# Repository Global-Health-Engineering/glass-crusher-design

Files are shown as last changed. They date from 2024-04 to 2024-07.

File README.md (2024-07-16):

<!-- badges: start -->


<!-- badges: end -->

<h1> Low-Cost Glass Crusher for Cape Maclear, Malawi: Design, Maintenance, Operation, and Results </h1>

<b>Contributors</b>  
- Philippe Colbach <a href="https://orcid.org/0009-0004-5631-8744">
ORCID logo 0009-0004-5631-8744
</a> *author, maintainer*  
- Jakub Tkaczuk <a href="https://orcid.org/0000-0001-7997-9423">
ORCID logo 0000-0001-7997-9423
</a> *supervisor, developer*  
- Elizabeth Tilley <a href="https://orcid.org/0000-0002-2095-9724">
ORCID logo 0000-0002-2095-9724
</a> *supervisor*  

<br>
<p align="middle"> 

<br><br>
This work is certified by the Open Source Hardware Association.<br \>

<br>
<b>Complete description of system design, functionalities, operation, and maintenance is available on:<br \>
<a href="https://global-health-engineering.github.io/glass-crusher-design/">Github pages</a>.
</b>
<br><br>
It compliments the openly-accessible master’s thesis, available on the<br \>  
<a href="http://hdl.handle.net/20.500.11850/670971">ETH Research Collection</a>.
</p>

# Background

This repository details the construction, operation, and maintenance of the glass crusher built as part of a collaboration between the Malawian nonprofit organization, Sustainable Cape Maclear, and the Global Health Engineering Group at ETH Zürich.

Sustainable Cape Maclear has been working on the development and implementation of a solid waste management strategy to address the village’s struggle with waste build-up at informal dumpsites. The desired outcome is an improved quality of life for the community and the preservation of the village’s status quo as one of the country’s major tourist destinations. To support the effort, the glass crusher, described in this repository, was designed, constructed and tested as a part of the Master's thesis.

After evaluating already established glass crusher variants, the design of choice became a manually driven roller mill. During testing, the drivetrain proved to be a major weak point. Due to its insufficient structural strength, the crusher was unable to crush intact glass bottles. However, breaking the bottles first and inserting their shards into the crusher worked well, producing particles of various sizes ranging from powder to several centimeters. Therefore, a second and more basic crusher, not described in this repository but detailed in the thesis, was built to take over the initial bottle-breaking task. The latter can serve as a standalone crusher, if large shard sizes are sufficient, or it can be combined with the original crusher, if smaller sizes are desired. In hindsight, it would have been better to build a more basic and robust crusher right from the start to circumvent many of the issues that arose. Overall, the current system is nonetheless capable of processing the village’s daily amount of waste glass within an acceptable time frame.

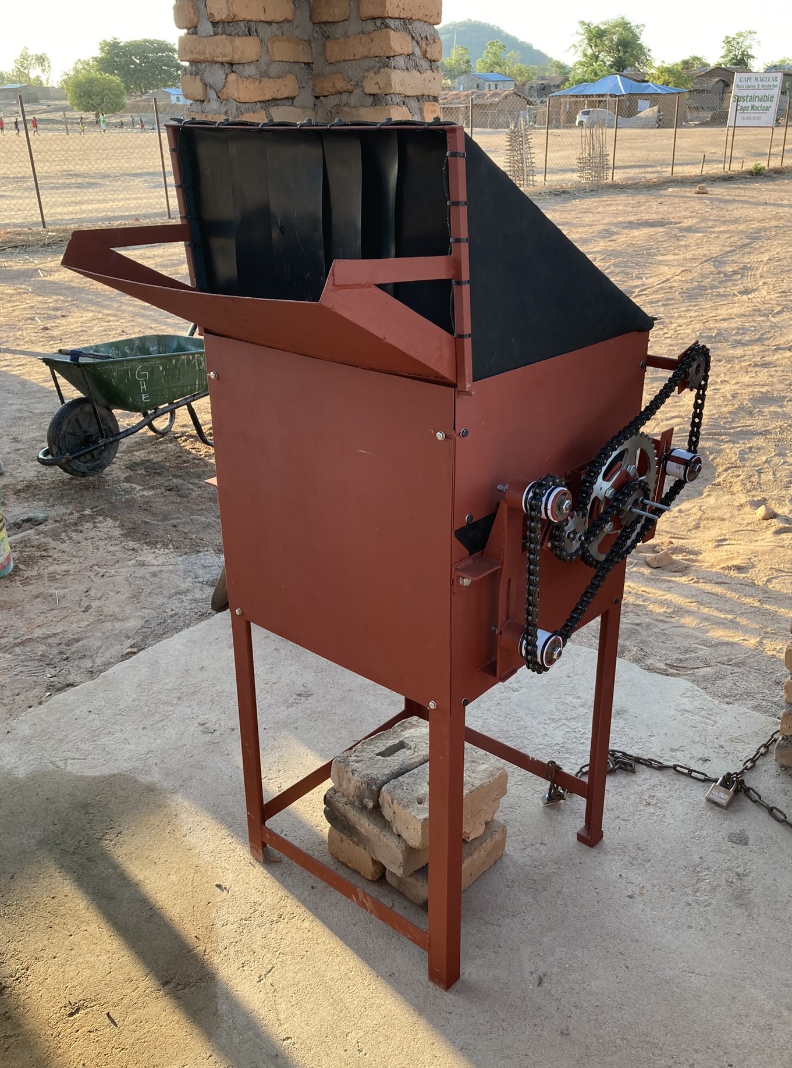
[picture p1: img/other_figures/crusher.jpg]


# pdf Documentation

All drawings necessary for the glass crusher construction are available in a pdf form in `pdf_doc/Glass_Crusher_Complete_Collection_of_Technical_Drawings.pdf`.

# License

The complete design and user manual are licensed under [Creative Commons Attribution 4.0 International](https://github.com/Global-Health-Engineering/glass-crusher-design/blob/main/LICENSE.md).

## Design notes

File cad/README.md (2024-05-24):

# cad

Directory containing CAD drawings in `.stp`, `.prt`, and `.pdf` formats.

| `dir` name | Description |
| --- | --- |
| `A_Glass_Crusher_Full_Assembly.*` | Final assembly of the glass crusher in three formats |
| `standard_parts` | Drawings of standard parts, e.g., screws, nuts, washers |
| `sub-assemblies` | All subassemblies used in `A_Glass_Crusher_Full_Assembly.stp` |
| `sub-assemblies/cover` | Drawings of the crusher's cover |
| `sub-assemblies/extended_frame` | Drawings of the assembled, extended frame |
| `sub-assemblies/motorcycle_chains` | Drawings of the motorcycle chain |
| `sub-assemblies/roller_mounting_platform` | Drawings of the roller mounting platform |
| `sub-assemblies/rollers` | Drawings of the rollers |
| `sub-assemblies/sprocket_module_large` | Drawings of the large sprocket module |
| `sub-assemblies/sprocket_module_small` | Drawings of the small sprocket module |
| `sub-assemblies/upper_side_panels` | Drawings of the upper side panels |

Each directory with an assembly contains the `parts` directory with the simplest part drawings.

# tree

    .
    ├── A_Glass_Crusher_Full_Assembly.prt
    ├── A_Glass_Crusher_Full_Assembly.stp
    ├── A_Glass_Crusher_Full_Assembly_dwg.pdf
    ├── standard_parts
    └── sub-assemblies
        ├── cover
        │   └── parts
        ├── extended_frame
        │   ├── parts
        │   └── subassemblies
        │       ├── crank
        │       │   └── parts
        │       ├── crank_side_panel
        │       │   └── parts
        │       ├── drivetrain_panel
        │       │   ├── parts
        │       │   └── subassemblies
        │       │       └── chain_guides
        │       │           └── parts
        │       └── frame
        │           └── parts
        ├── motorcycle_chains
        │   └── subassemblies
        │       └── chain_subunits
        │           └── parts
        ├── roller_mounting_platform
        │   └── parts
        ├── rollers
        │   ├── parts
        │   └── subassemblies
        │       └── roller_bearing_brackets
        │           └── parts
        ├── sprocket_module_large
        │   └── parts
        ├── sprocket_module_small
        │   └── parts
        └── upper_side_panels
            └── parts

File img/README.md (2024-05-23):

# img

This directory contains images grouped into following sub-directories:

| `dir` name | Description |
| --- | --- |
| `drawings` | Engineering drawings of parts and assemblies |
| `other_figures` | Figures and photographs for technical documentation |

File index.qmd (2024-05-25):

---
title: "Low-Cost Glass Crusher for Cape Maclear, Malawi"
subtitle: "Design, Maintenance, Operation, and Results"
number-sections: true
format: html
---

<!-- badges: start -->


<!-- badges: end -->

<b>Contributors:</b>  
- Philippe Colbach <a href="https://orcid.org/0009-0004-5631-8744">
ORCID logo 0009-0004-5631-8744
</a> *author, maintainer*  
- Jakub Tkaczuk <a href="https://orcid.org/0000-0001-7997-9423">
ORCID logo 0000-0001-7997-9423
</a> *supervisor, developer*  
- Elizabeth Tilley <a href="https://orcid.org/0000-0002-2095-9724">
ORCID logo 0000-0002-2095-9724
</a> *supervisor*  

<br>
<p align="middle">

<br><br> This work is certified by the Open Source Hardware
Association.\
(https://certification.oshwa.org/ch000022.html)
<br>
Github repository for this page sits [here](https://github.com/Global-Health-Engineering/glass-crusher-design).
</p>

# Introduction {#sec-intro}

This documentation details the construction, operation, and maintenance of the glass crusher that was built as part of a collaboration between the Malawian nonprofit organization Sustainable Cape Maclear and the Global Health Engineering Group at ETH Zürich.

# Prototype Overview {#sec-overview}

The glass crusher uses two roller mills to crush the glass. The rollers are rotated using a crank and a drivetrain made mostly from motorcycle parts. It is a mostly closed construction to shield the operator(s) from glass dust and shards.

Figure 1: Complete assembly of the glass crusher.

During testing, it became clear that the crusher was not strong enough to break intact glass bottles. Therefore, an additional pre-crusher was built to break the bottles first before inserting their shards into the main crusher for further refinement.

Unless explicitly stated otherwise, all information in this documentation relates to the main glass crusher, not the pre-crusher.

# Part List {#sec-list}

| Material | Units | Unit Cost (MWK) | Total Cost (MWK) | Total Cost (USD) | Notes |
| :--- | ---: | ---: | ---: | ---: | --- |
| Anti-Rust Coating <br> 1 L | 1 | 26'000 | 26'000 | 14.77 | |
| Bearing 6206 RS <br> Ø<sub>i</sub> 30 mm | 2 | 9'000 | 18'000 | 10.23 | |
| Bearing 6304 2RS <br> Ø<sub>i</sub> 20 mm | 2 | 8'000 | 16'000 | 9.09 | |
| Damp-proof course <br> 0.25 mm x 100 mm x 40'000 mm | 1 | 4'950 | 4'950 | 2.81 | |
| Durable rubber sheet <br> 2 mm x 1'500 mm x 2'600 mm | 1 | 70'000 | 70'000 | 39.77 | |
| Galvanized steel elbow connector <br> Ø<sub>i</sub> 15 mm | 2 | 1'024 | 2'048 | 1.16 | |
| Galvanized steel pipe <br> Ø<sub>i</sub> 15 mm x Ø<sub>o</sub> 20 mm x 1'000 mm | 1 | 16'174 | 16'174 | 9.19 | |
| Galvanized steel pipe <br> Ø<sub>i</sub> 15 mm x Ø<sub>o</sub> 20 mm x 300 mm | 2 | 5'044 | 10'088 | 5.73 | |
| Galvanized steel round cap <br> Ø<sub>i</sub> 15 mm | 1 | 734 | 734 | 0.42 | |
| L-profile <br> 5 mm x 40 mm x 40 mm x 5'800 mm | 1 | 39'500 | 39'500 | 22.44 | |
| Motorcycle Chain <br> Size 520 x 66 links (minimum) | 2 | 70'000 | 140'000 | 79.55 | |
| Motorcycle Sprocket <br> Size 520 x 13T | 3 | 28'000 | 84'000 | 47.73 | |
| Motorcycle Sprocket <br> Size 520 x 42T | 1 | 65'000 | 65'000 | 36.93 | |
| PVC pipe <br> Ø<sub>i</sub> 22 mm x Ø<sub>o</sub> 25 mm x 3'000 mm | 1 | 3'300 | 3'300 | 1.88 | |
| PVC straight pipe connector <br> Øi 50 mm x 50 mm | 3 | 1'200 | 3'600 | 2.05 | |
| Screws, nuts, and washers[^1] | 1 | 49'600 | 49'600 | 28.18 | |
| Steel bar flat <br> 2.75 mm x 20 mm x 5'800 mm | 1 | 6'000 | 6'000 | 3.41 | |
| Steel corner bracket <br> 2.5 mm x 50 mm x 50 mm x 20 mm | 1 | 604 | 604 | 0.34 | |
| Steel flat bar <br> 5 mm x 40 mm x 5'800 mm | 1 | 45'000 | 45'000 | 25.57 | |
| Steel pipe <br> Ø<sub>o</sub> 43 mm x 1'000 mm | 1 | 0 | 0 | 0.00 | scrap part |
| Steel roller <br> Ø<sub>o</sub> 150 mm x 500 mm | 2 | 209'700 | 419'400 | 238.30 | |
| Steel sheet <br> 2 mm x 1'300 mm x 3'350 mm | 1 | 250'000 | 250'000 | 142.05 | |
| Steel sheet <br> 3 mm x  350 mm x 400 mm | 1 | 0 | 0 | 0.00 | scrap part |
| Steel square tubing <br> 1.15 mm x 15 mm x 15 mm x 5'800 mm | 2 | 4'950 | 9'900 | 5.63 | |
| Zip ties | 33 | 0 | 0 | 0.00 | scrap part |
|  |  | **TOTAL COST** | **1'279'898** | **727.21** | |

[^1]: 24 x screw M6 x 16, 1 x screw M6 x 20, 2 x screw M6 x 25, 12 x screw M6 x 30, 4 x screw M6 x 45, 2 x stud M6 x 20, 53 x nut M6, 67 x washer M6, 5 x screw M10 x 20 <br> 12 x screw M10 x 30, 1 x stud M10 x 90, 2 x stud M10 x 120, 23 x nut M10, 19 x washer M10

# Safety Precautions {#sec-safety}

Always wear protective equipment when working with glass. A mask, goggles, gloves and closed footwear are essential for protecting the operator’s health.

# License {#sec-license}

The complete design and user manual are licensed under [Creative Commons Attribution 4.0 International](https://github.com/Global-Health-Engineering/glass-crusher-design/blob/main/LICENSE.md).

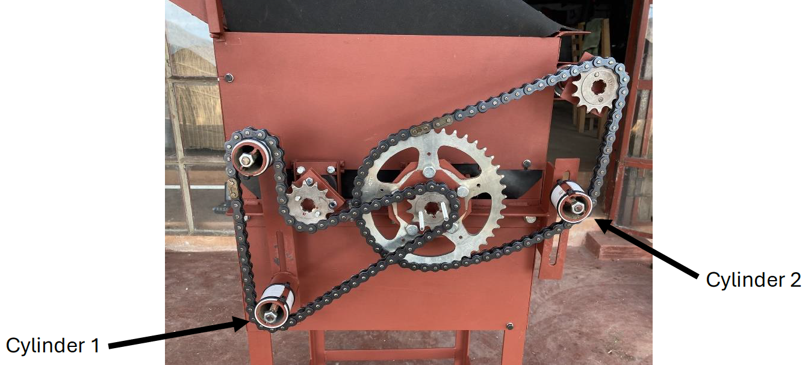
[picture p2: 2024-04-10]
docs/img/schematics/chain-replacement-cylinders.png

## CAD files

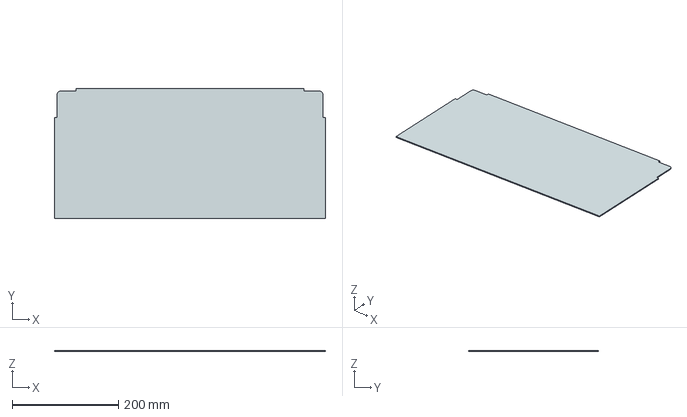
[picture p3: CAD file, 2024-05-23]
cad/sub-assemblies/extended_frame/subassemblies/frame/parts/M_Bot_Funnel_Panel_Main.stp
510.0 x 245.0 x 2.00 mm

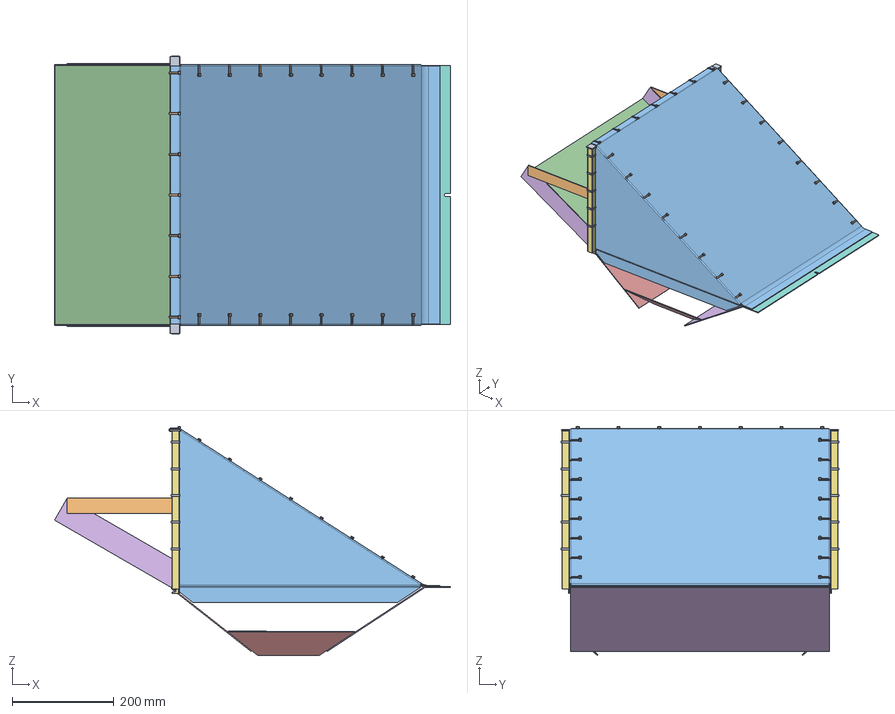
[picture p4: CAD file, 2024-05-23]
cad/sub-assemblies/cover/A_Cover.stp
779.5 x 547.0 x 450.8 mm
M_Zip_Tie_Symbolic_Square x 10
M_Zip_Tie_Symbolic_Flat x 23
FlatPattern_Geometry x 7
M_Top_Funnel_Side x 2
M_Chute_Side x 2
M_Cover_Support_Mirror
M_Top_Funnel_Support
M_Cover_Crossbar
M_Chute_Support x 2
M_Cover_Strut x 2
M_Chute_Plate
M_Cover_Support
M_Top_Funnel_Plate_S
M_Top_Funnel_Plate_L

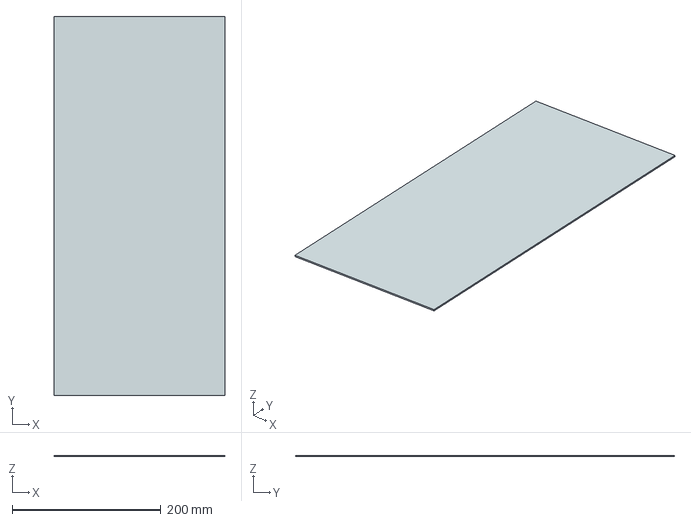
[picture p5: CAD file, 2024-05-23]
cad/sub-assemblies/cover/parts/M_Top_Funnel_Plate_L.stp
230.0 x 510.0 x 2.00 mm

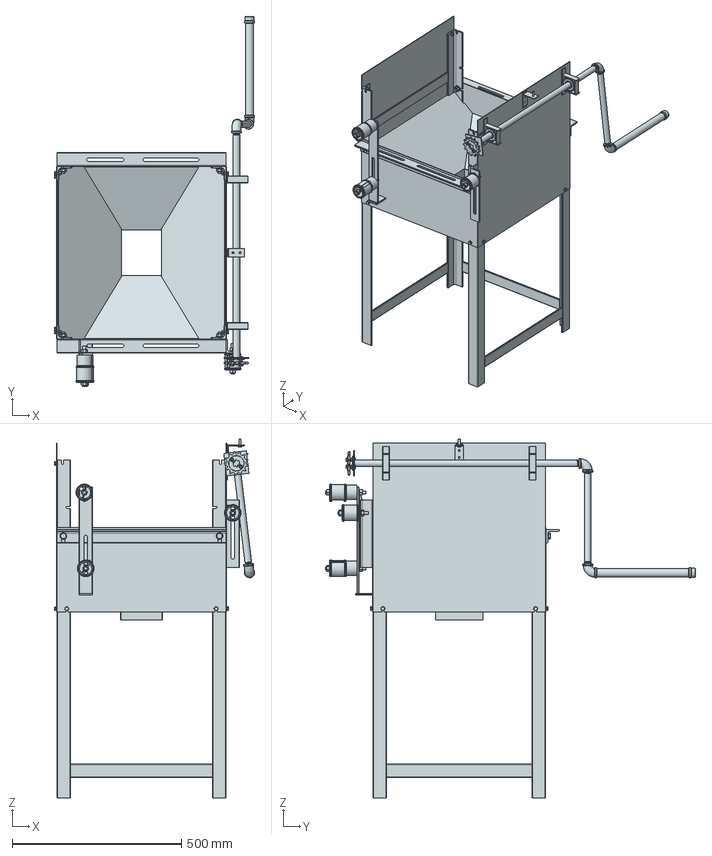
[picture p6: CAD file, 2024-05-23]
cad/sub-assemblies/extended_frame/A_Extended_Frame.stp
592.2 x 1095.2 x 1062.0 mm
Hex Nut, 1A, DIN,M10x1_5 x 10
Plain Washer, Normal, DIN,M10 x 11
Hex Head Screw, Grades A, B, DIN,M10x30 x 4
Hex Nut, 1A, DIN,M6x1 x 16
Plain Washer, Normal, DIN,M6 x 24
Hex Head Screw, Grades A, B, DIN,M6x16 x 12
M_Roller_Mounting_Platform_Slit_Insert x 4
M_Roller_Mounting_Platform
M_Crank_Handle_Cap
M_Crank_Handle_Sleeve
M_Crank_Shaft
M_Sprocket_S_Plate_Crank
M_Crank_Arm_and_Handle x 2
M_Crank_Connector x 2
Hex Head Screw, Grades A, B, DIN,M6x25 x 2
Plain Washer, DIN 440,M6 x 2
M_Sprocket_S
M_Side_Panel_S_Bot x 2
M_Side_Panel_L x 2
M_Roller_Mounting_Platform_Mirror
M_Zip_Tie_Symbolic_Circular x 6
M_Chain_Guide_Sleeve x 3
M_Chain_Guide_Connector_S x 2
M_Chain_Guide_Pipe_S
Stud, Form A, DIN,M10x1_5x90
M_Chain_Guide_Pipe_L x 2
M_Chain_Guide_Connector_L x 4
Stud, Form A, DIN,M10x1_5x120 x 2
M_Chain_Guide_Mounting_Bar
M_Chain_Guide_Mounting_Bar_Support_Bot
M_Chain_Guide_Mounting_Bar_Support_Top
M_Chain_Guide_Mounting_Corner_Profile
Hex Head Screw, Grades A, B, DIN,M6x20
M_Corner_Bracket
M_Corner_Bracket_Spacer
M_Bearing_Bracket_S_Base x 2
M_Bearing_Bracket_S_Top x 2
M_Bearing_Bracket_S_Side x 4
Single Row Radial Contact Ball Brg, 2RS W 2 Seals, DIN,6304_2RS x 2
M_Frame_Connecting_Bar_L x 4
M_Frame_Connecting_Bar_S
M_Frame_Corner_Profile x 2
M_Frame_Corner_Profile_Mirror x 2
M_Bot_Funnel_Extension_L x 2
M_Bot_Funnel_Extension_S x 2
M_Bot_Funnel_Panel_Main x 2
M_Bot_Funnel_Panel_Side x 2

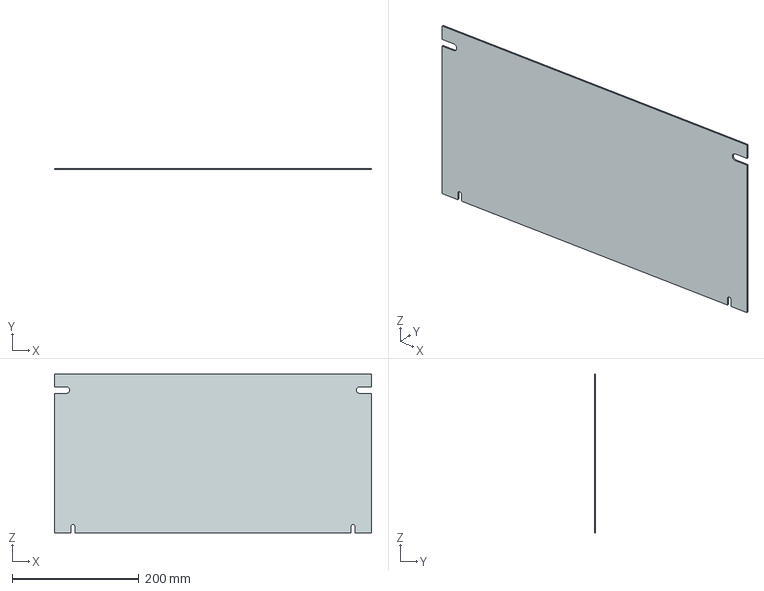
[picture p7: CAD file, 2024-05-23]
cad/sub-assemblies/extended_frame/parts/M_Side_Panel_S_Bot.stp
500.0 x 2.00 x 250.0 mm

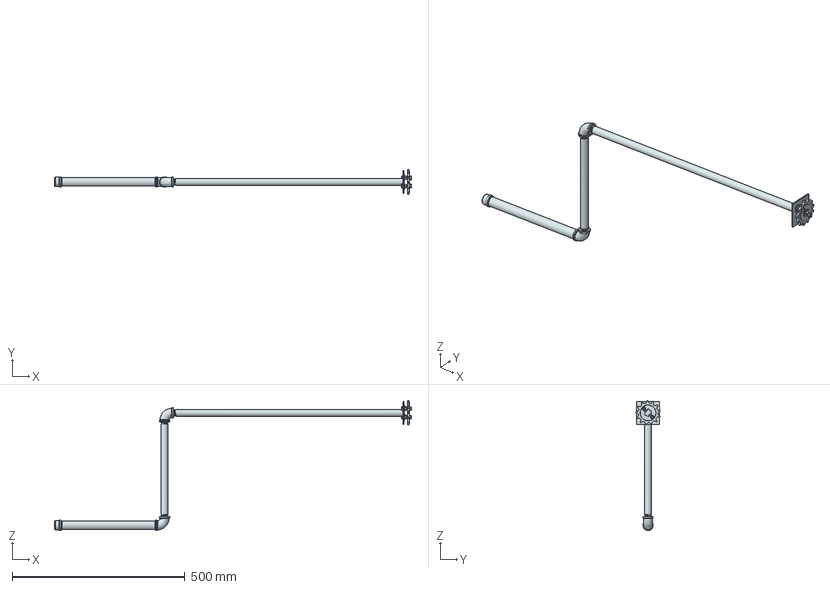
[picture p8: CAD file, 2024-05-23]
cad/sub-assemblies/extended_frame/subassemblies/crank/A_Crank.stp
1034.5 x 71.6 x 377.0 mm
Hex Nut, 1A, DIN,M6x1 x 4
M_Sprocket_S
Plain Washer, DIN 440,M6 x 2
Hex Head Screw, Grades A, B, DIN,M6x25 x 2
M_Crank_Connector x 2
M_Crank_Arm_and_Handle x 2
M_Sprocket_S_Plate_Crank
M_Crank_Shaft
M_Crank_Handle_Sleeve
M_Crank_Handle_Cap

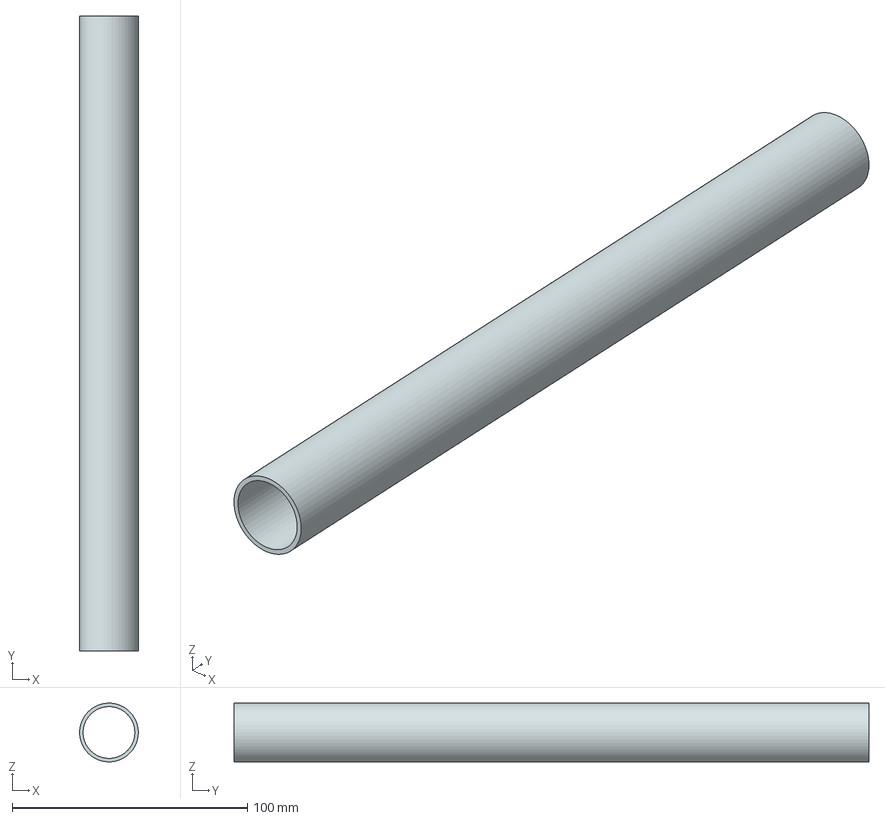
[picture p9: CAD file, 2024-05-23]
cad/sub-assemblies/extended_frame/subassemblies/crank/parts/M_Crank_Handle_Sleeve.stp
25.0 x 270.0 x 25.0 mm

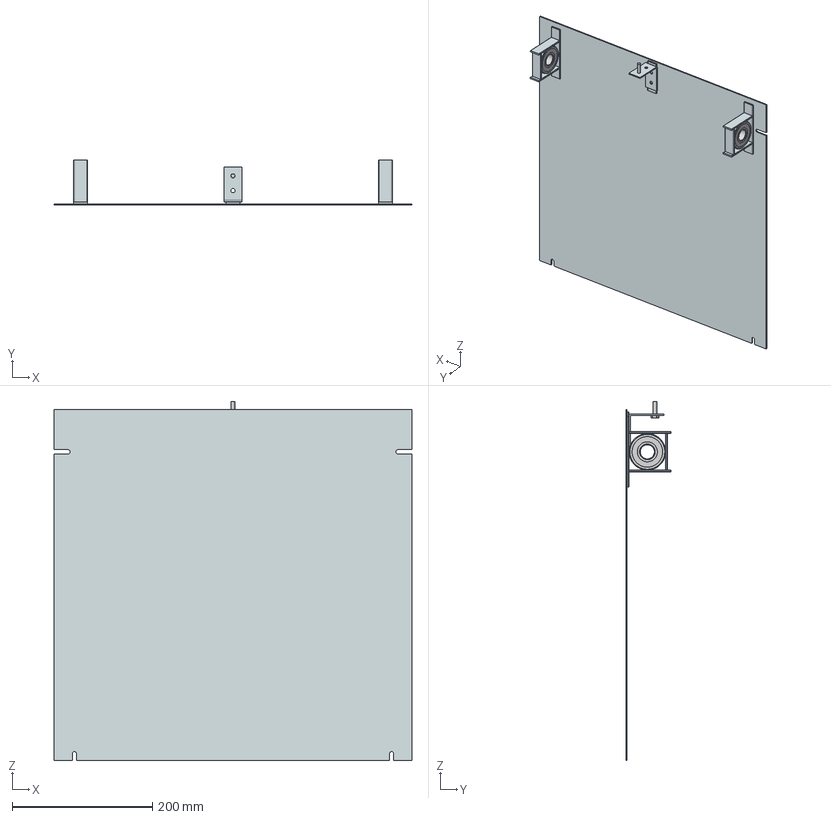
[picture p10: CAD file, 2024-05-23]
cad/sub-assemblies/extended_frame/subassemblies/crank_side_panel/A_Crank_Side_Panel.stp
510.0 x 64.8 x 512.0 mm
Hex Head Screw, Grades A, B, DIN,M6x20
Single Row Radial Contact Ball Brg, 2RS W 2 Seals, DIN,6304_2RS x 2
M_Bearing_Bracket_S_Side x 4
M_Bearing_Bracket_S_Top x 2
M_Bearing_Bracket_S_Base x 2
M_Side_Panel_L
M_Corner_Bracket_Spacer
M_Corner_Bracket

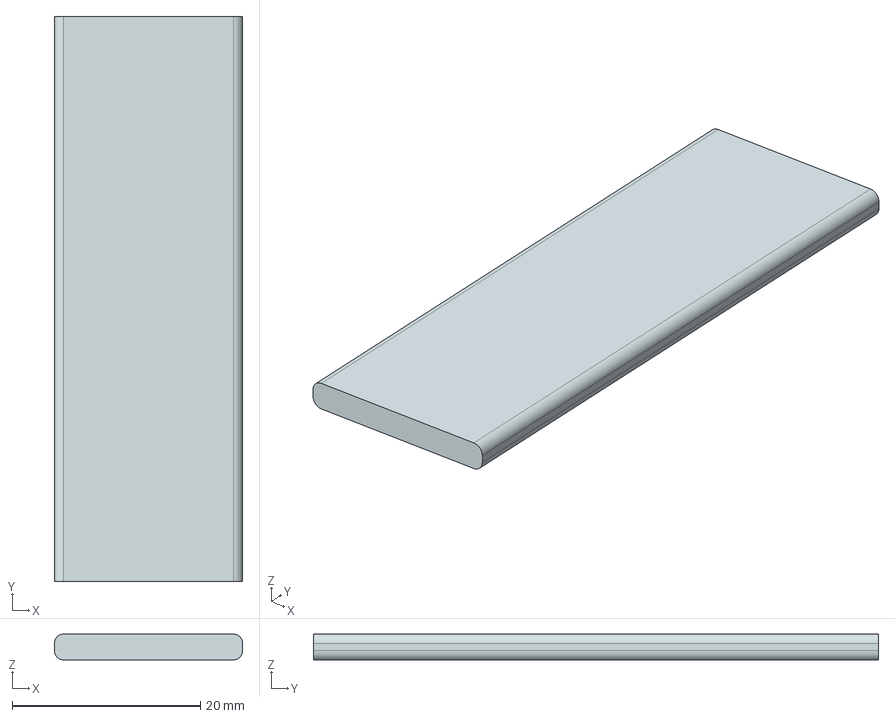
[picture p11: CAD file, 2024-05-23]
cad/sub-assemblies/extended_frame/subassemblies/crank_side_panel/parts/M_Bearing_Bracket_S_Side.stp
20.0 x 60.0 x 2.75 mm

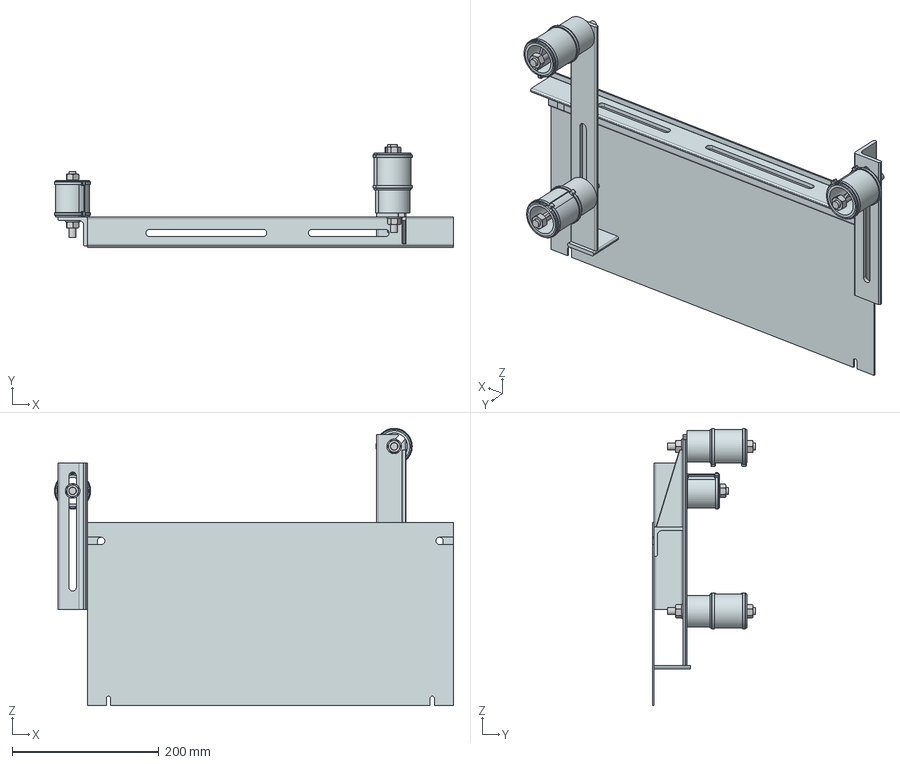
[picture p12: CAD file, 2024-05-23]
cad/sub-assemblies/extended_frame/subassemblies/drivetrain_panel/A_Side_Panel_S_Bot_Drivetrain.stp
544.7 x 141.0 x 378.7 mm
Plain Washer, Normal, DIN,M10 x 3
Hex Nut, 1A, DIN,M10x1_5 x 6
M_Roller_Mounting_Platform_Mirror
M_Zip_Tie_Symbolic_Circular x 6
M_Chain_Guide_Sleeve x 3
M_Chain_Guide_Connector_S x 2
M_Chain_Guide_Pipe_S
Stud, Form A, DIN,M10x1_5x90
M_Chain_Guide_Pipe_L x 2
M_Chain_Guide_Connector_L x 4
Stud, Form A, DIN,M10x1_5x120 x 2
M_Roller_Mounting_Platform_Slit_Insert x 2
M_Side_Panel_S_Bot
M_Chain_Guide_Mounting_Corner_Profile
M_Chain_Guide_Mounting_Bar_Support_Top
M_Chain_Guide_Mounting_Bar_Support_Bot
M_Chain_Guide_Mounting_Bar

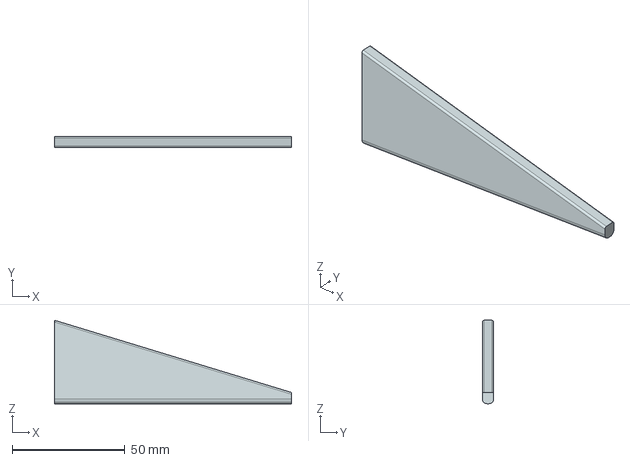
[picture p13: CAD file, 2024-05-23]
cad/sub-assemblies/extended_frame/subassemblies/drivetrain_panel/parts/M_Chain_Guide_Mounting_Bar_Support_Top.stp
105.0 x 5.00 x 37.0 mm

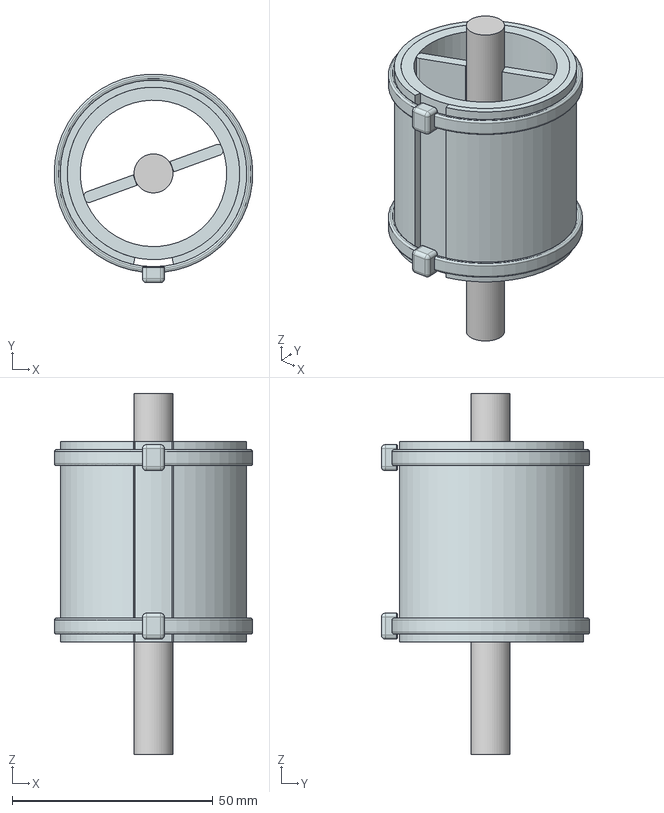
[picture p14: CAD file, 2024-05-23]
cad/sub-assemblies/extended_frame/subassemblies/drivetrain_panel/subassemblies/chain_guides/A_Chain_Guide_S.stp
49.5 x 52.0 x 90.0 mm
M_Zip_Tie_Symbolic_Circular x 2
M_Chain_Guide_Sleeve
Stud, Form A, DIN,M10x1_5x90
M_Chain_Guide_Connector_S x 2
M_Chain_Guide_Pipe_S

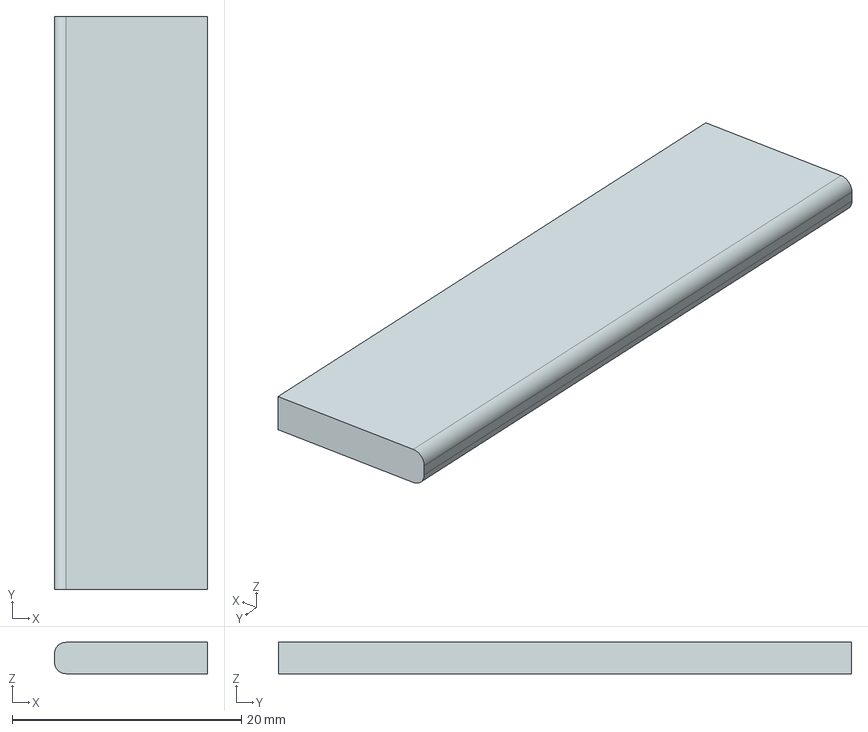
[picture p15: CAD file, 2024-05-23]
cad/sub-assemblies/extended_frame/subassemblies/drivetrain_panel/subassemblies/chain_guides/parts/M_Chain_Guide_Connector_S.stp
13.3 x 50.0 x 2.75 mm

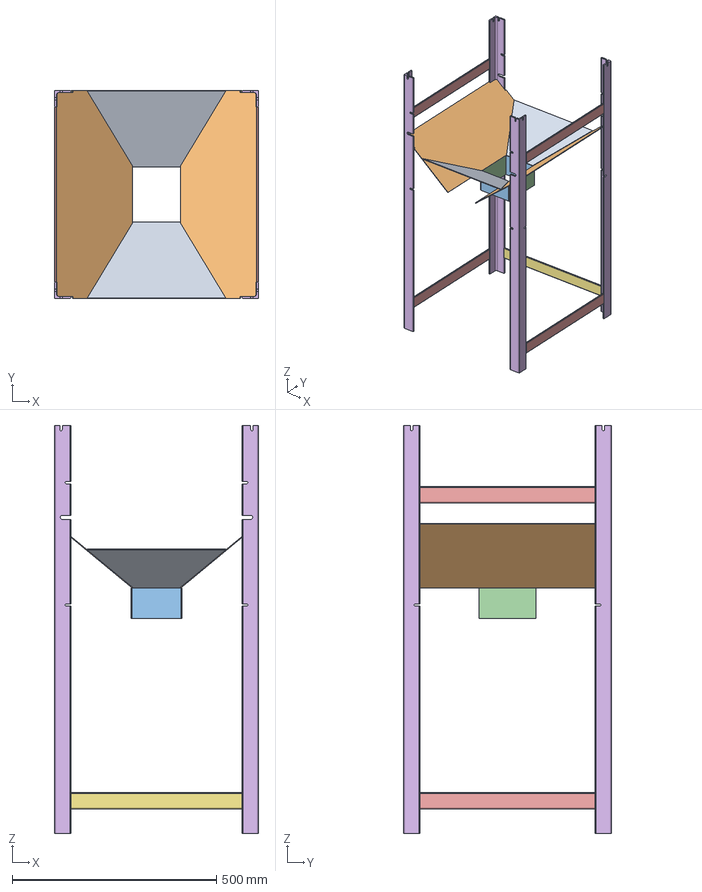
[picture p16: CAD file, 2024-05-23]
cad/sub-assemblies/extended_frame/subassemblies/frame/A_Frame.stp
500.0 x 510.0 x 1000.0 mm
M_Bot_Funnel_Panel_Side x 2
M_Bot_Funnel_Panel_Main x 2
M_Bot_Funnel_Extension_S x 2
M_Bot_Funnel_Extension_L x 2
M_Frame_Connecting_Bar_L x 4
M_Frame_Corner_Profile_Mirror x 2
M_Frame_Corner_Profile x 2
M_Frame_Connecting_Bar_S

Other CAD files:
cad/sub-assemblies/extended_frame/subassemblies/frame/parts/M_Frame_Connecting_Bar_L.stp
cad/sub-assemblies/motorcycle_chains/A_Motorcycle_Chain_Crank_Roller.stp
cad/sub-assemblies/motorcycle_chains/subassemblies/chain_subunits/A_Motorcycle_Chain_Unit_Outer.stp
cad/sub-assemblies/motorcycle_chains/subassemblies/chain_subunits/parts/M_Motorcycle_Chain_Roller.stp
cad/A_Glass_Crusher_Full_Assembly.prt
cad/standard_parts/Hex_Head_Screw_Grades_A_B_DIN_M10x20.stp
cad/standard_parts/Hex_Head_Screw_Grades_A_B_DIN_M10x30.stp
cad/standard_parts/Hex_Head_Screw_Grades_A_B_DIN_M6x16.stp
cad/standard_parts/Hex_Head_Screw_Grades_A_B_DIN_M6x20.stp
cad/standard_parts/Hex_Head_Screw_Grades_A_B_DIN_M6x25.stp
cad/standard_parts/Hex_Head_Screw_Grades_A_B_DIN_M6x30.stp
cad/standard_parts/Hex_Head_Screw_Grades_A_B_DIN_M6x45.stp
cad/standard_parts/Hex_Nut_1A_DIN_M10x1_5.stp
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

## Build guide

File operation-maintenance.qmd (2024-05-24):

---
title: "Prototype Operation & Maintenance"
number-sections: true
format: html
---

# Prototype Operation {#sec-operation}

## Standard Operating Procedure {#sec-sop}

1. Put a bucket underneath the crusher. Place it as high up as possible by stacking bricks under it.
2. Throw in the glass through the chute. Avoid putting in too much at a time.
3. Slowly turn the crank. If there is a noticeable resistance buildup, do not force the crank further. Instead, rotate it backward a bit, then go forward again. It might be necessary to repeat this multiple times. If this does not solve the issue, refer to the section *What if the machine jams?*.
4. Once all the glass has been crushed, the bucket can be removed.

## Changing the Roller Gap {#sec-changing-roller-gap}

The design was originally conceived in a way that allows the roller closest to the crank to be moved back and forth. The idea was that by adjusting the roller gap, different sizes of glass could be crushed and produced. Doing so involves the following steps:

1. Loosen chain guides 1 & 2 (see Figure 1).
2. Loosen the four bolts that are used to fasten the roller’s bearing brackets to their respective platform. The two bolts on the drivetrain side can be difficult to access; using an L-shaped hex socket wrench with a long shaft is recommended.
3. Move the roller to adjust the gap from wide to narrow or vice versa.
4. Refasten the bearing bracket bolts.
5. Slide the chain guides downwards to put tension on the chain. Make sure the chain is in contact with the plastic sleeves and fasten the chain guides.
6. Pull on the chain to check if it is not too loose, then turn the crank to make sure that there is not too much tension either. If necessary, readjust.

**IMPORTANT NOTE**: The wider setting ultimately proved to be completely ineffective at crushing intact glass bottles—the sole reason it was included as a design feature in the first place; hence, the glass crusher ended up being used exclusively on the narrowest setting. The usefulness and effectiveness of the wider setting is thus not guaranteed.

Figure 1. Chain tightening cylinders - loosen to change the roller gap or replace the chain.

# Prototype Maintenance {#sec-maintenance}

## Regular Maintenance {#sec-reg-maintenance}

Grease the chain and sprockets as needed to ensure a smooth operation.

At some point, it might additionally be necessary to replace one of the two 520 motorcycle chains or the chain guide sleeves. To do so, proceed as follows:

1. Loosen chain guides 1 & 2 (see Figure 1) and slide them upwards.
2. With the chain tension removed, the chain or the chain guide sleeves can be removed and replaced.
3. After the replacement is done, slide the chain guides back downwards to put tension on the chain. Make sure the chain is in contact with the plastic sleeves and fasten the chain guides.
4. Pull on the chain to check if it is not too loose, then turn the crank to make sure that there is not too much tension either. If necessary, readjust.

## What if the machine jams? {#sec-jam}

If something jams the machine, it usually suffices to reach into the crusher and remove the piece that is causing the jam by hand. Make sure that no other person is using the crusher in the meantime. If possible, firmly hold the crank with your free hand to make sure the rollers do not start moving on their own.

If the issue is not solvable by reaching in through the top, the top structure is designed to be removable. To do so, proceed as follows:

1. Remove the screw nut at the back.
2. Rotate the top upwards.
3. Once rotated, slide it off the two pins at the front and the top has been successfully removed.

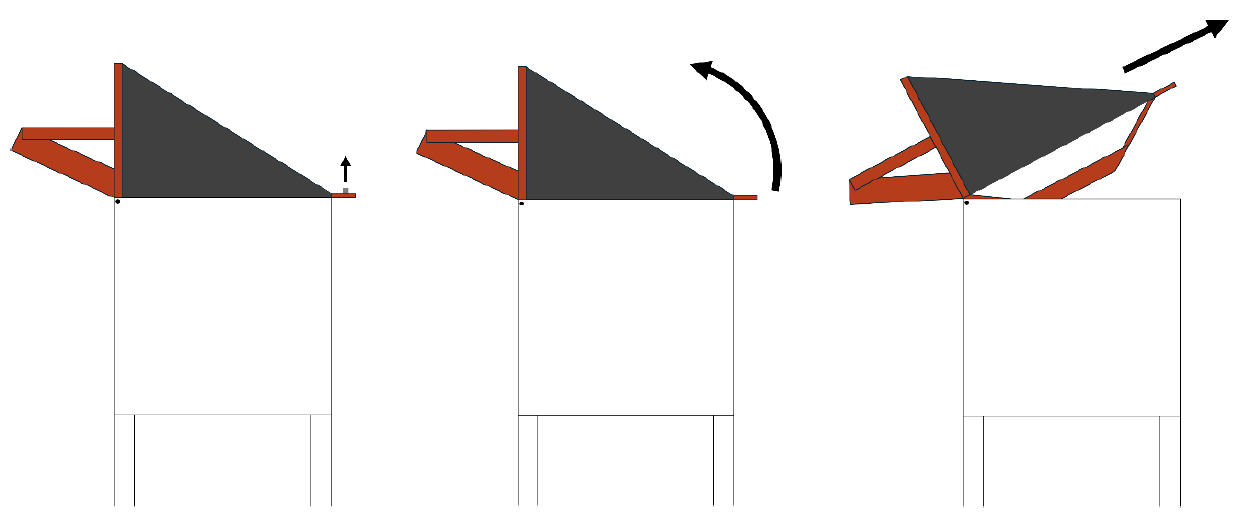
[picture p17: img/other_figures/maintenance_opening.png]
Figure 2. Procedure for removing the top.


To put it back, follow the same procedure in reverse:

1. Place the front of the cover structure into the crusher and make sure the two hooks slide onto their respective pin.
2. Rotate the top’s rear down onto the screw.
3. Put the nut back onto the screw.

**Note**: It is possible to almost entirely disassemble the glass crusher, but it is highly recommended not to do so unless absolutely necessary.

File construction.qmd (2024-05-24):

---
title: "Prototype Construction"
number-sections: true
format: html
---

# Overview {#sec-overview}

The technical drawings should provide enough information on their own to reproduce the parts. These instructions therefore assume that the reader has already prepared all the parts and that the only remaining step is their assembly. They furthermore assume that the reader wants to make an identical copy of the crusher; due to dimensional dependencies, any modification made to one part may negatively affect how well, if at all, others are going to fit.

It should be noted that some of the assembly instructions might be difficult to reproduce without assistance from a second person.

# Sub-assemblies {#sec-sub-assemblies}

## Base Frame {#sec-base-frame}

Start by welding the connecting bars (1) & (8) to the corner profiles (6) & (7) - numbered parts shown in Figure 2. Weld the main funnel panels (3) to the corner profiles, then add the funnel’s side panels (2) and the extensions (4) & (5). Make sure to leave enough space between the funnel panels (3) and the M10 screw slits on the corner profiles (6) & (7) so that it is still possible to fit in an M10 nut later.

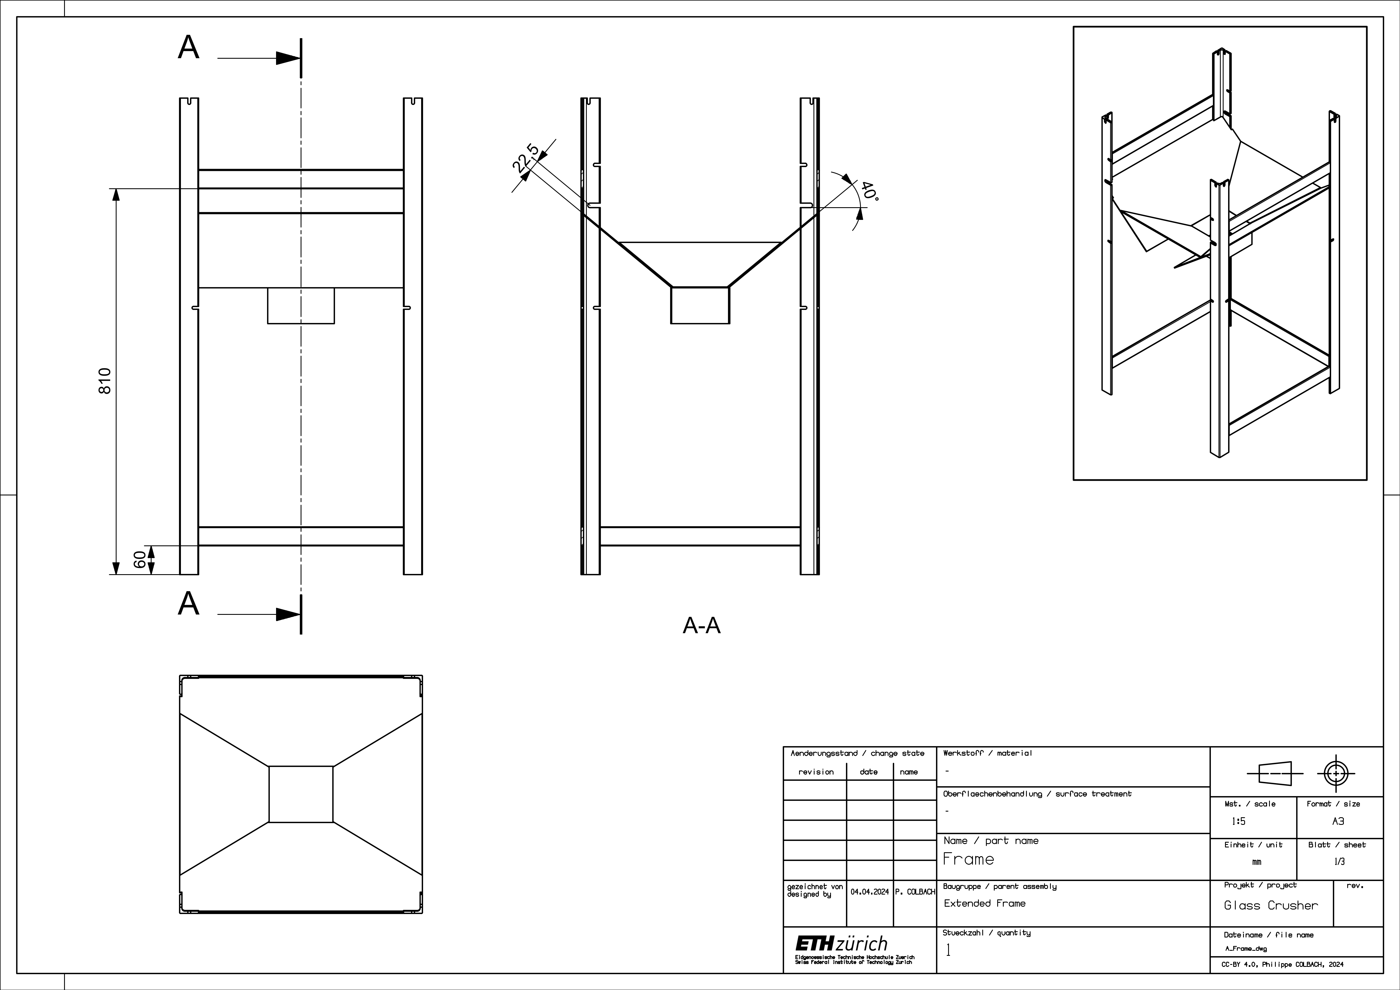
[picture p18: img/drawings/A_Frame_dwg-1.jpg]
Figure 1: Side views and a 3D view of the base frame.


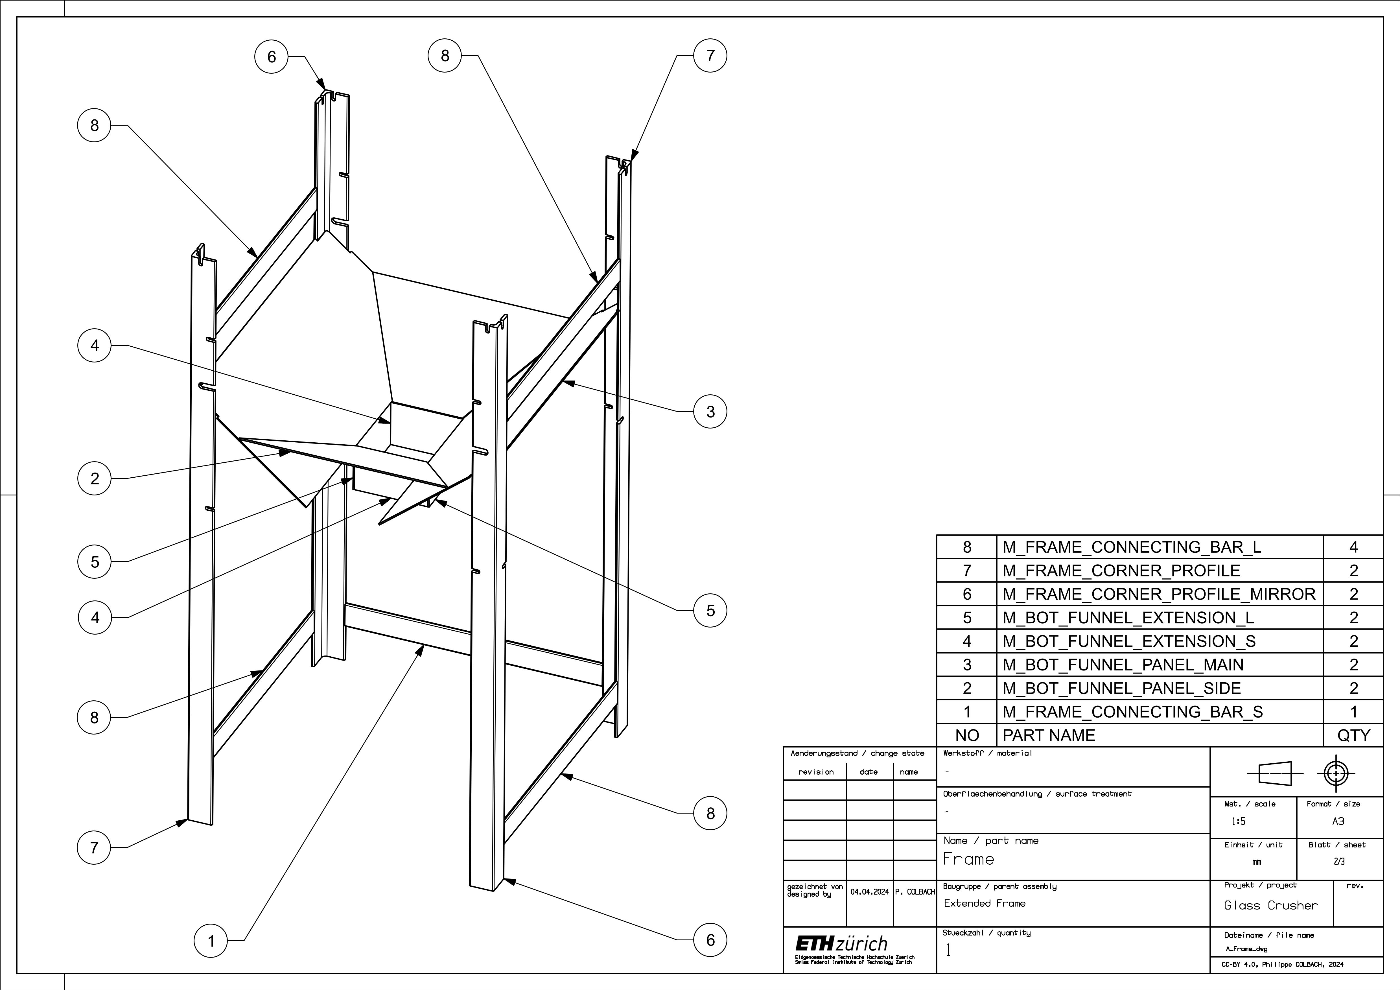
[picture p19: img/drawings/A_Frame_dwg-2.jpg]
Figure 2: Part list of the base frame.


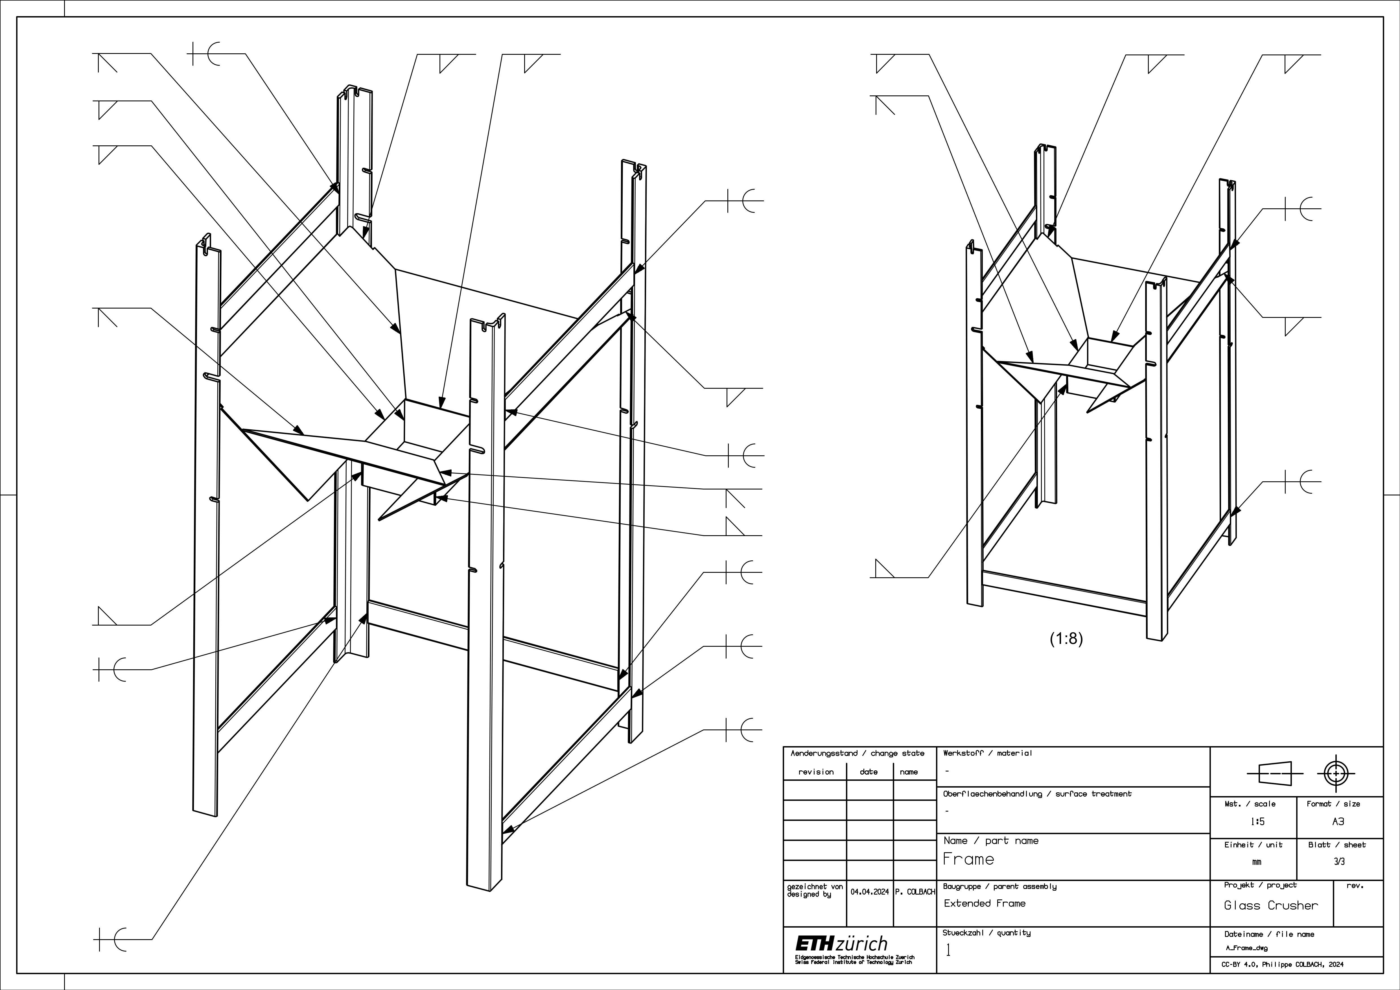
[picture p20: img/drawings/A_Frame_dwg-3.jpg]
Figure 3: Welding instructions for the base frame design.


## Crank {#sec-crank}

The crank consists mostly of pipes and pipe fittings screwed together, but a couple of welds are required. It is easiest to start with the latter. Weld the sprocket plate (3) onto the crank’s shaft (2) - numbered parts shown in Figure 4. Make sure the plate is centered relative to the pipe and remember to leave out the screw-adjacent sections, as there might not be enough space for the screw head (10) otherwise. Now the sprocket (1) can be mounted onto the plate and the rest of the pipes can be screwed onto the shaft. Do not forget to put the sleeve (4) over the crank’s handle (9), although it can easily be added later.

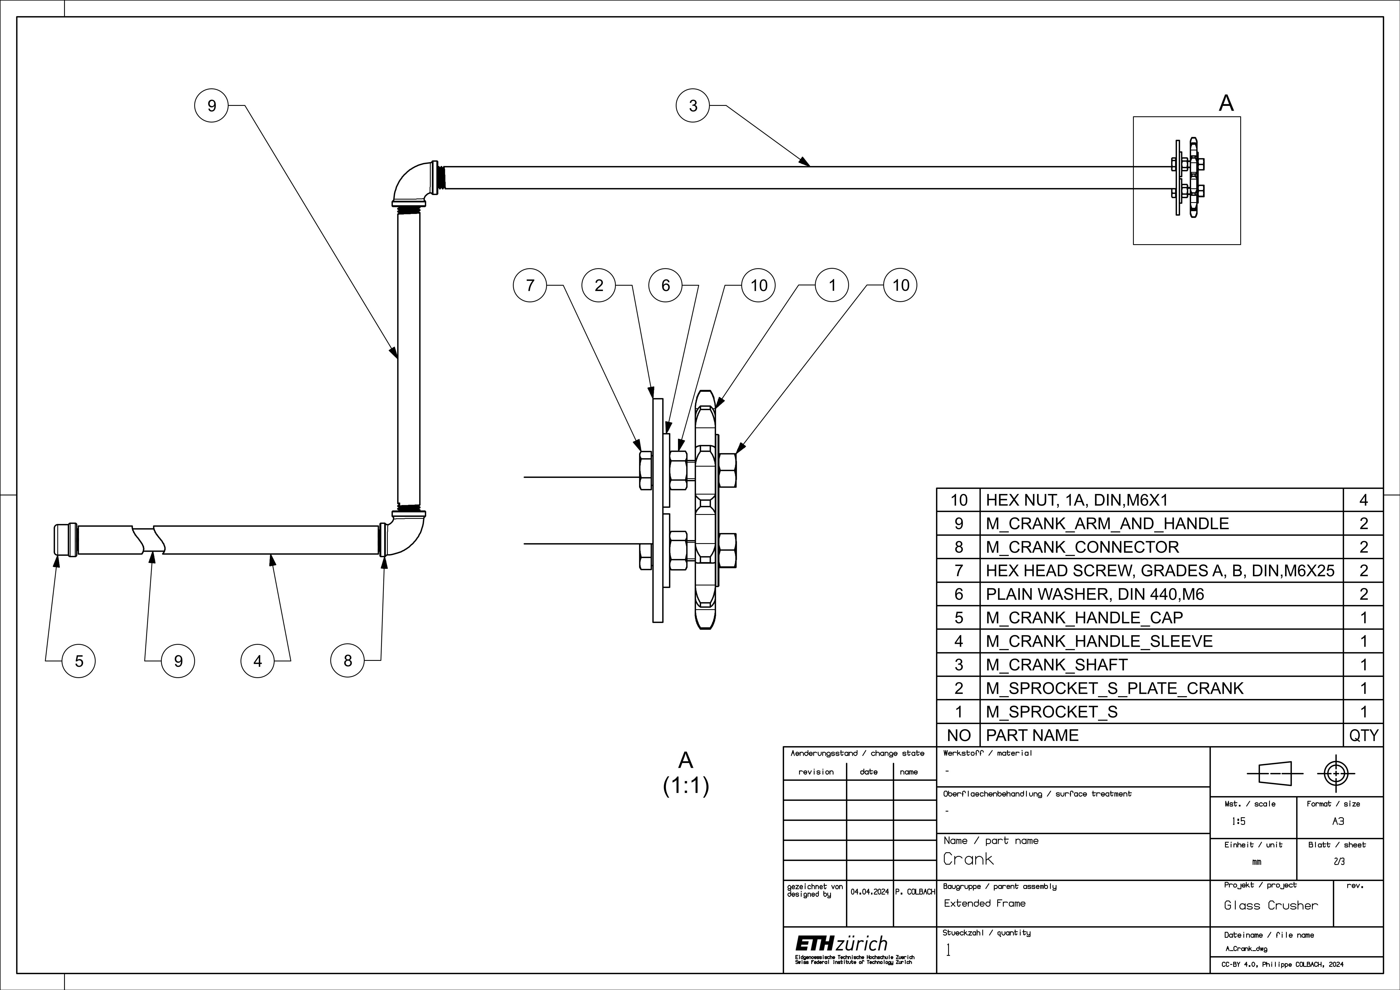
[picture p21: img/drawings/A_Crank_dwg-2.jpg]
Figure 4: Part list of the crank assembly.


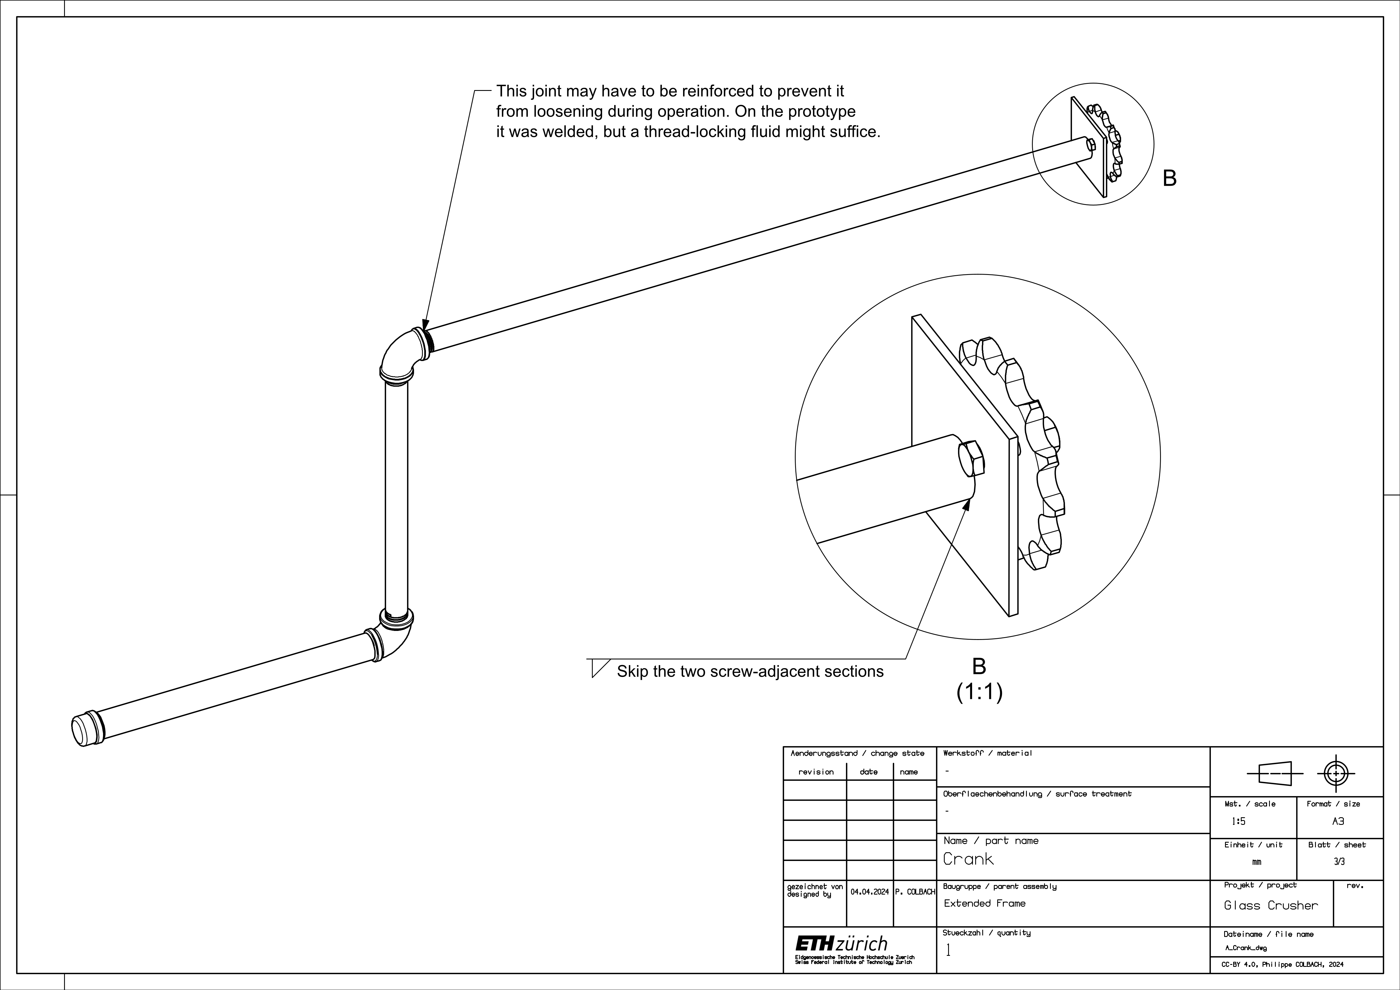
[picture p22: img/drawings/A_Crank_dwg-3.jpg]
Figure 5: Welding instructions for the crank.


## Crank Side Panel {#sec-crank-side-panel}

Weld the corner bracket (4), its spacer (3), and the stud (1) to the panel (2) - numbered parts shown in Figure 7. For the bearing brackets, either start by welding the bracket base (7) to the panel and then finish the bracket from there or build the brackets independently and weld them to the panel once they are finished. Either way, precision is key: A precise placement ensures a smooth drivetrain motion. 

It is equally important to weld the junction between the bracket base (7) and bracket side (8) on the inside first, and only afterwards on the outside, to make sure the side pieces are going to exert a clamping force on the bearing (5). Once the side pieces are welded, the best approach is to mount the bearings on the crank’s shaft first, then place them into their respective bracket and in a last step, add each bracket’s top piece (6). 

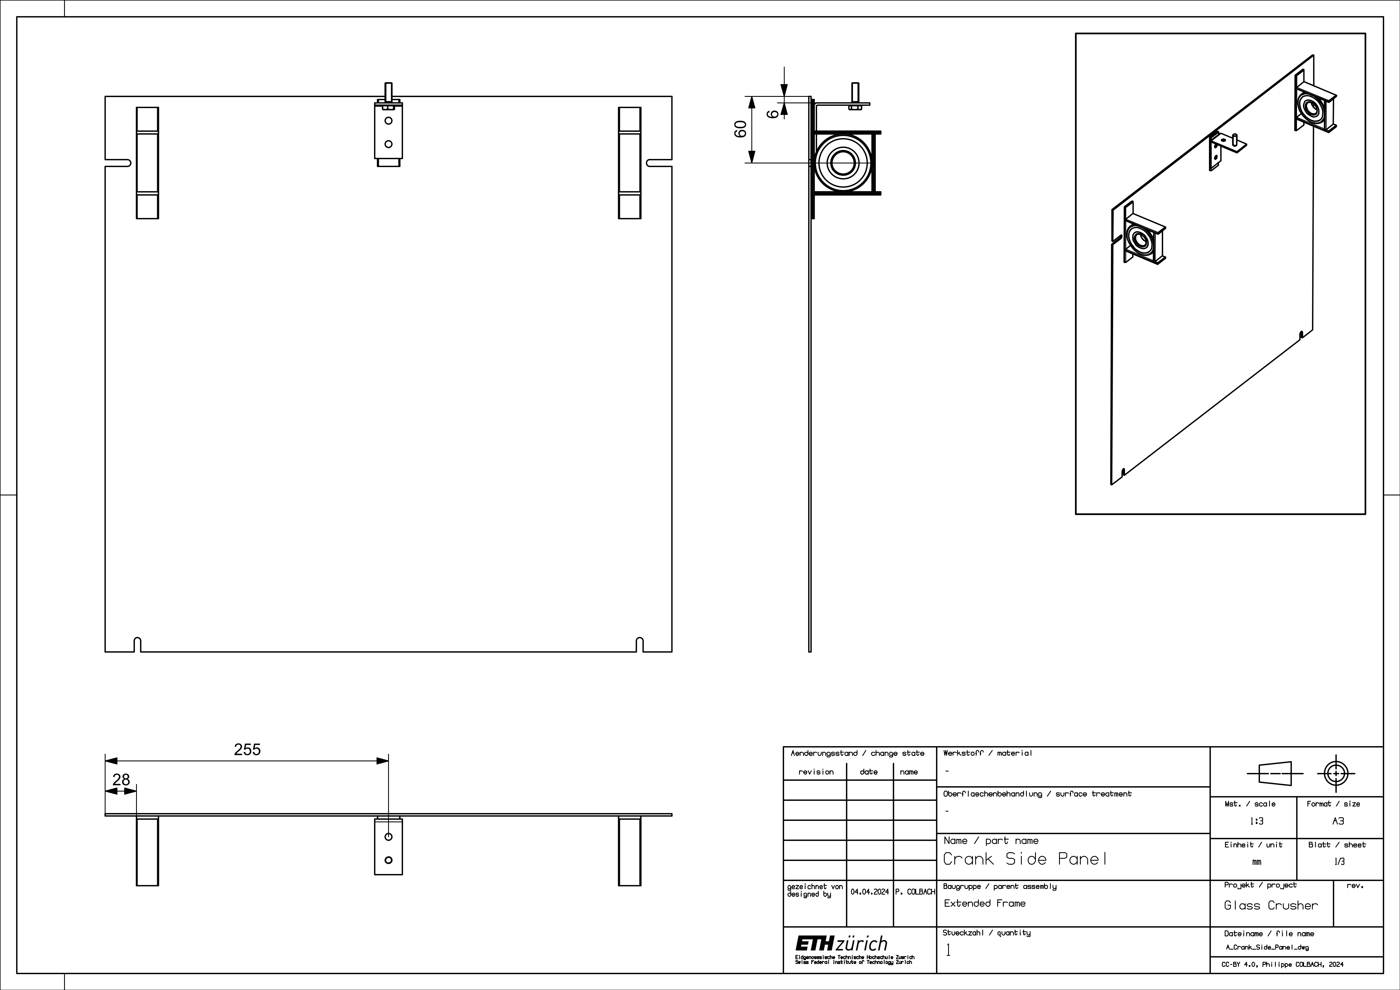
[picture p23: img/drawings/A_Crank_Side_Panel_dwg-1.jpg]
Figure 6: Side panel assembly.


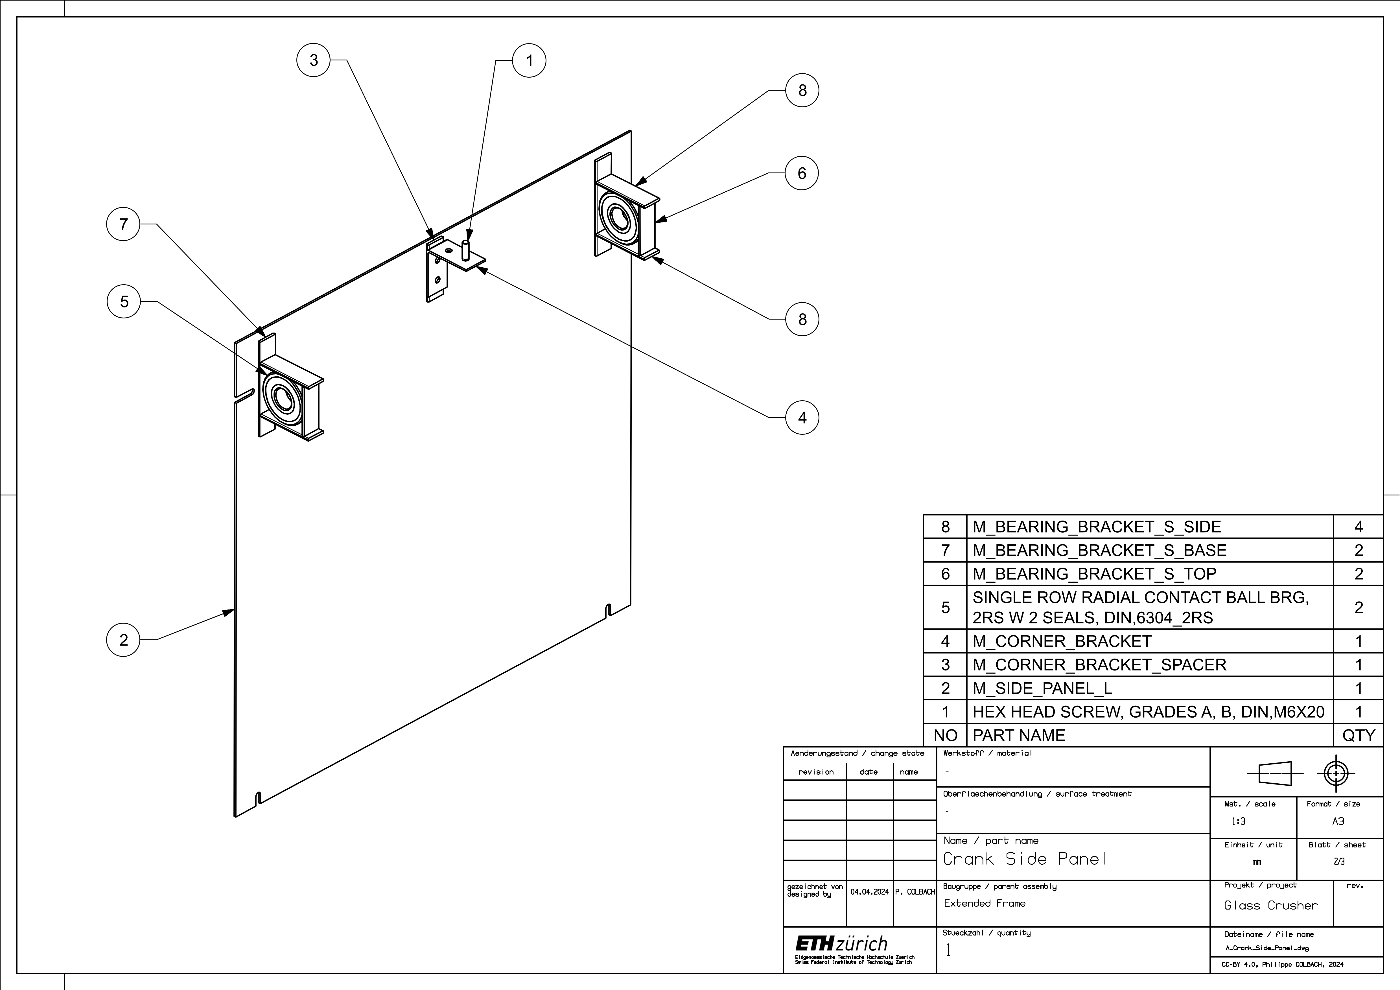
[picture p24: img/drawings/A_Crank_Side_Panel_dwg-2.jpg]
Figure 7: Part list of the side panel.


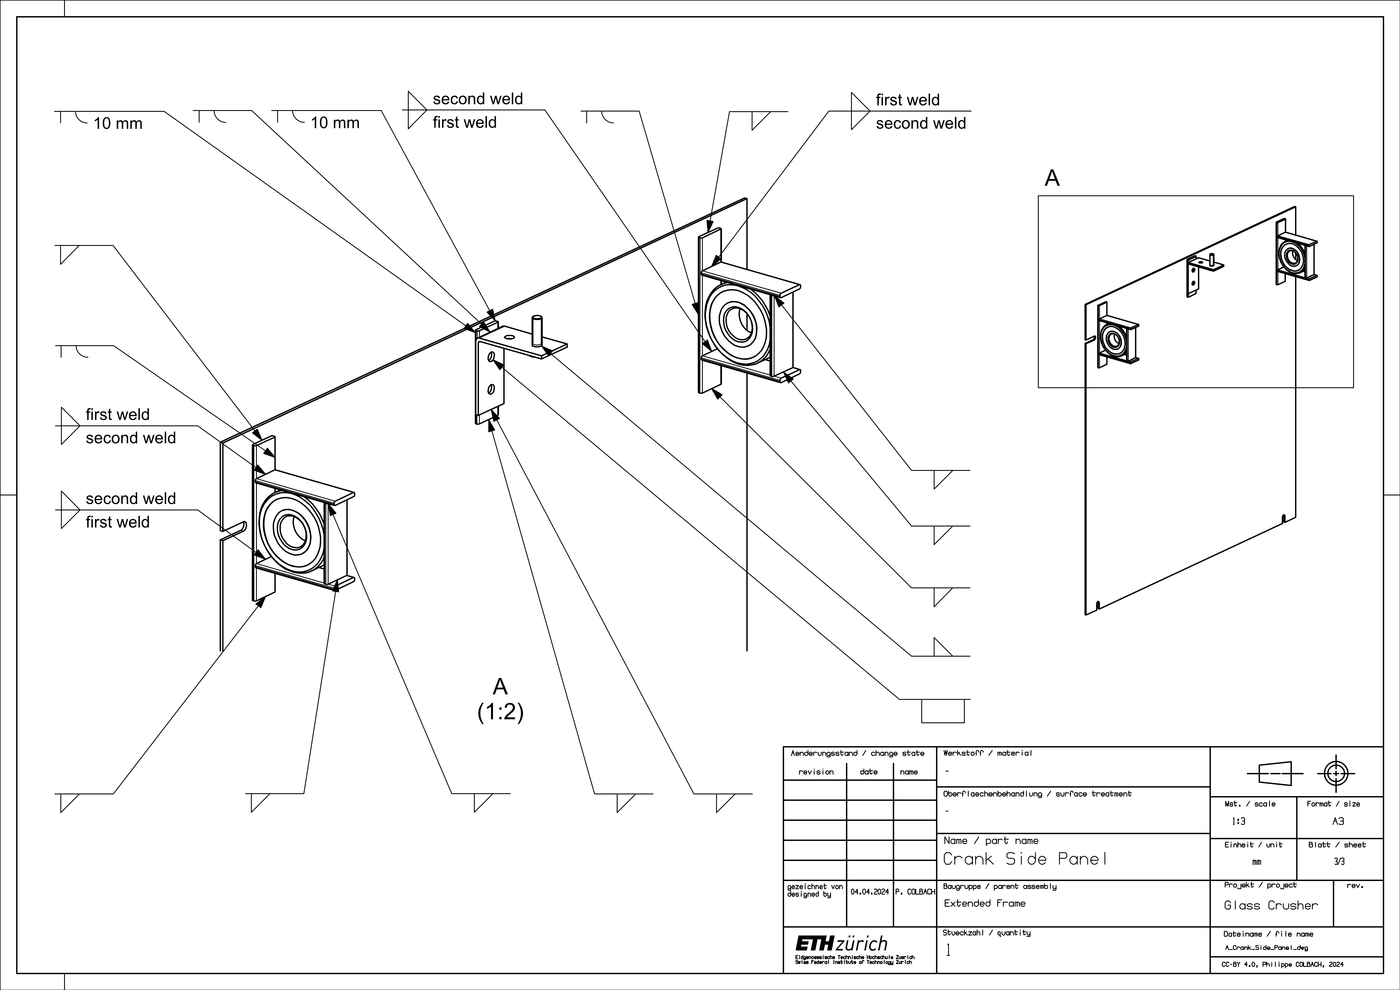
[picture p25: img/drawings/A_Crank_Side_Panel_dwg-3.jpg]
Figure 8: Welding instructions for the side panel.


## Chain Guides {#sec-chain-guides}

The long and short chain guides both follow the same assembly scheme, which is why only the short one’s is described here. Start by welding the connecting pieces (5) to the stud (2), then weld it to the pipe’s inner wall (3) - numbered parts shown in Figure 10. Add the sleeve (1) and fix it in place using two zip ties (4).

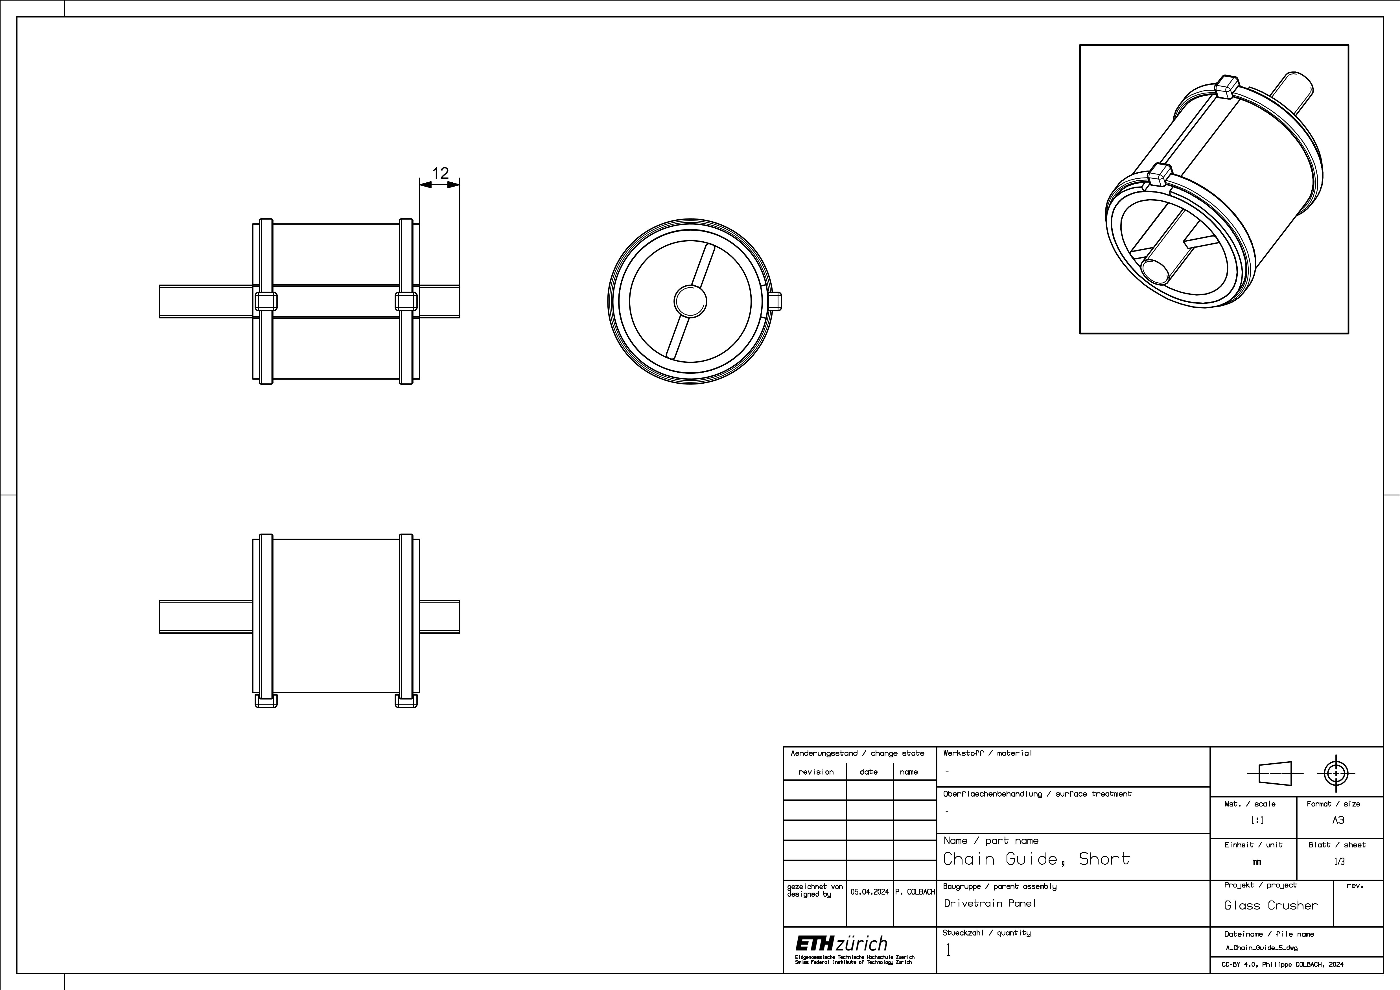
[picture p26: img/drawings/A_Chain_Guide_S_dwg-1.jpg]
Figure 9: Chain guide assembly.


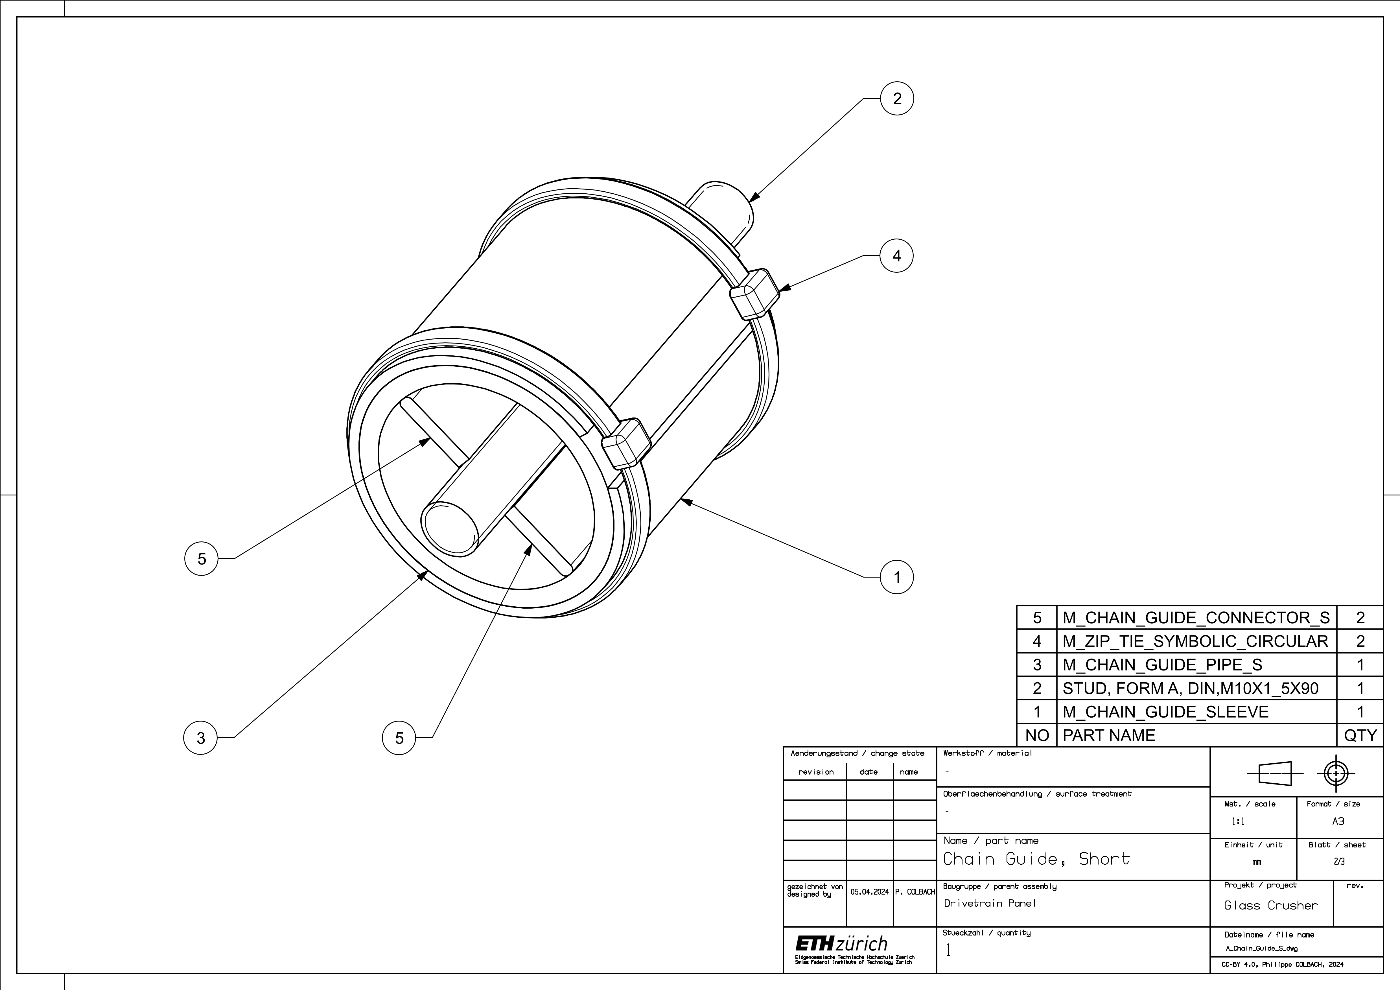
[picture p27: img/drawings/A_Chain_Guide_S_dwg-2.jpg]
Figure 10: Chain guide part list.


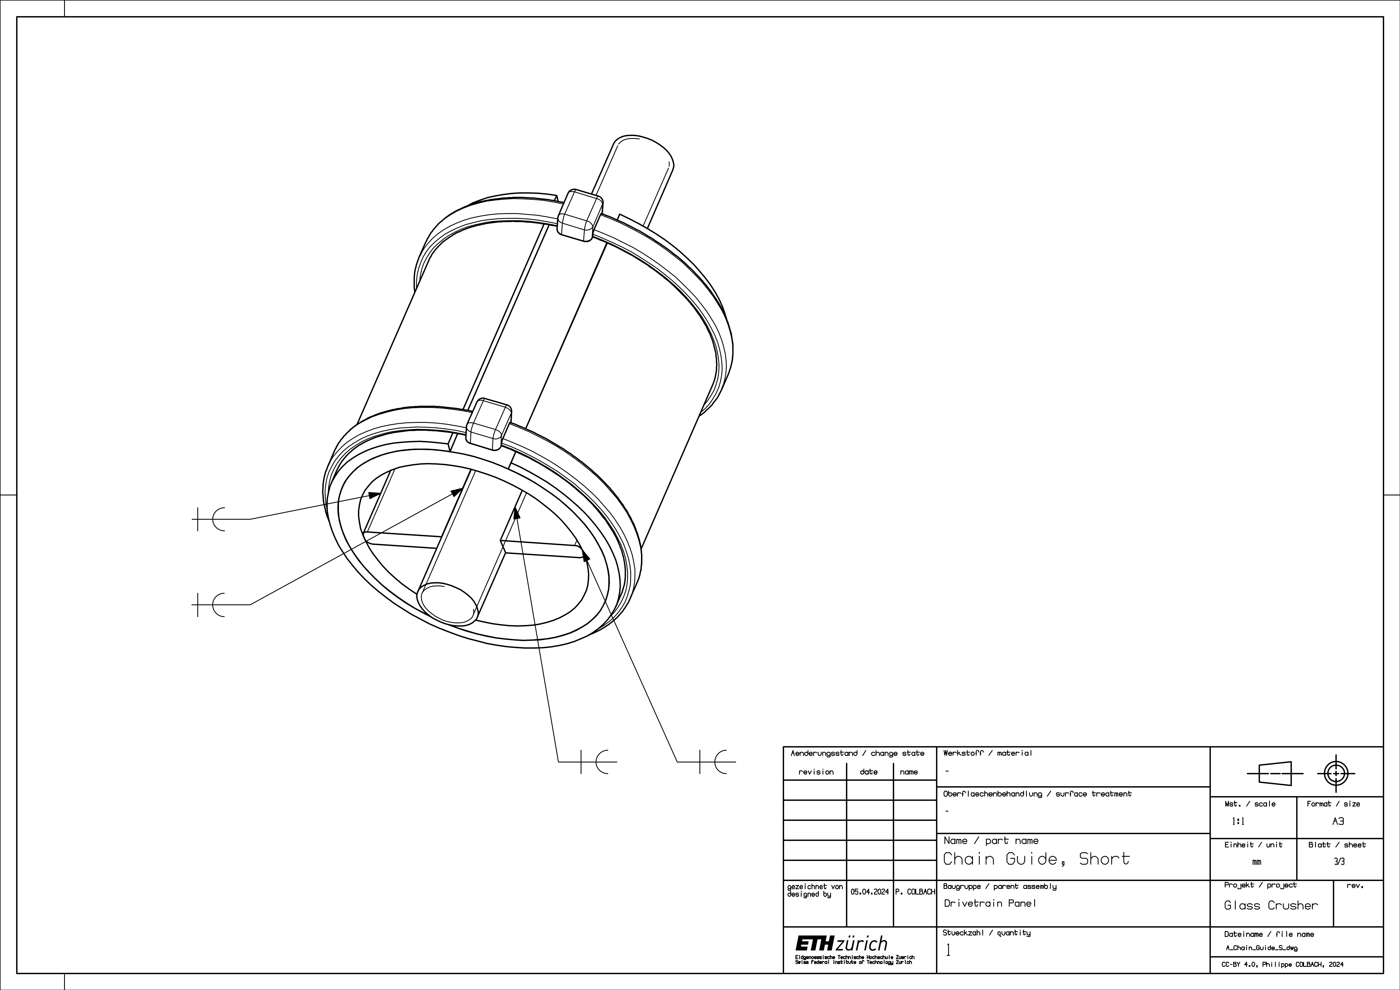
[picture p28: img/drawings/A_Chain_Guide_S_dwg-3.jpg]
Figure 11: Welding instructions for the chain guide assembly.


## Drivetrain Panel {#sec-drivetrain-panel}

Next up is the drivetrain panel. Start by welding the roller platform (9) to the panel (7) - numbered parts shown in Figure 13. Use two M10 screws to facilitate their alignment. Add the two inserts (9) and flatten the welds. Add the flat mounting bar (2), its supports (3) & (4), and the corner profile (5). Finish it up by installing the chain guides. Make sure to place the short one (1) into the corner profile (5), and the longer ones (8) into the flat bar (2).

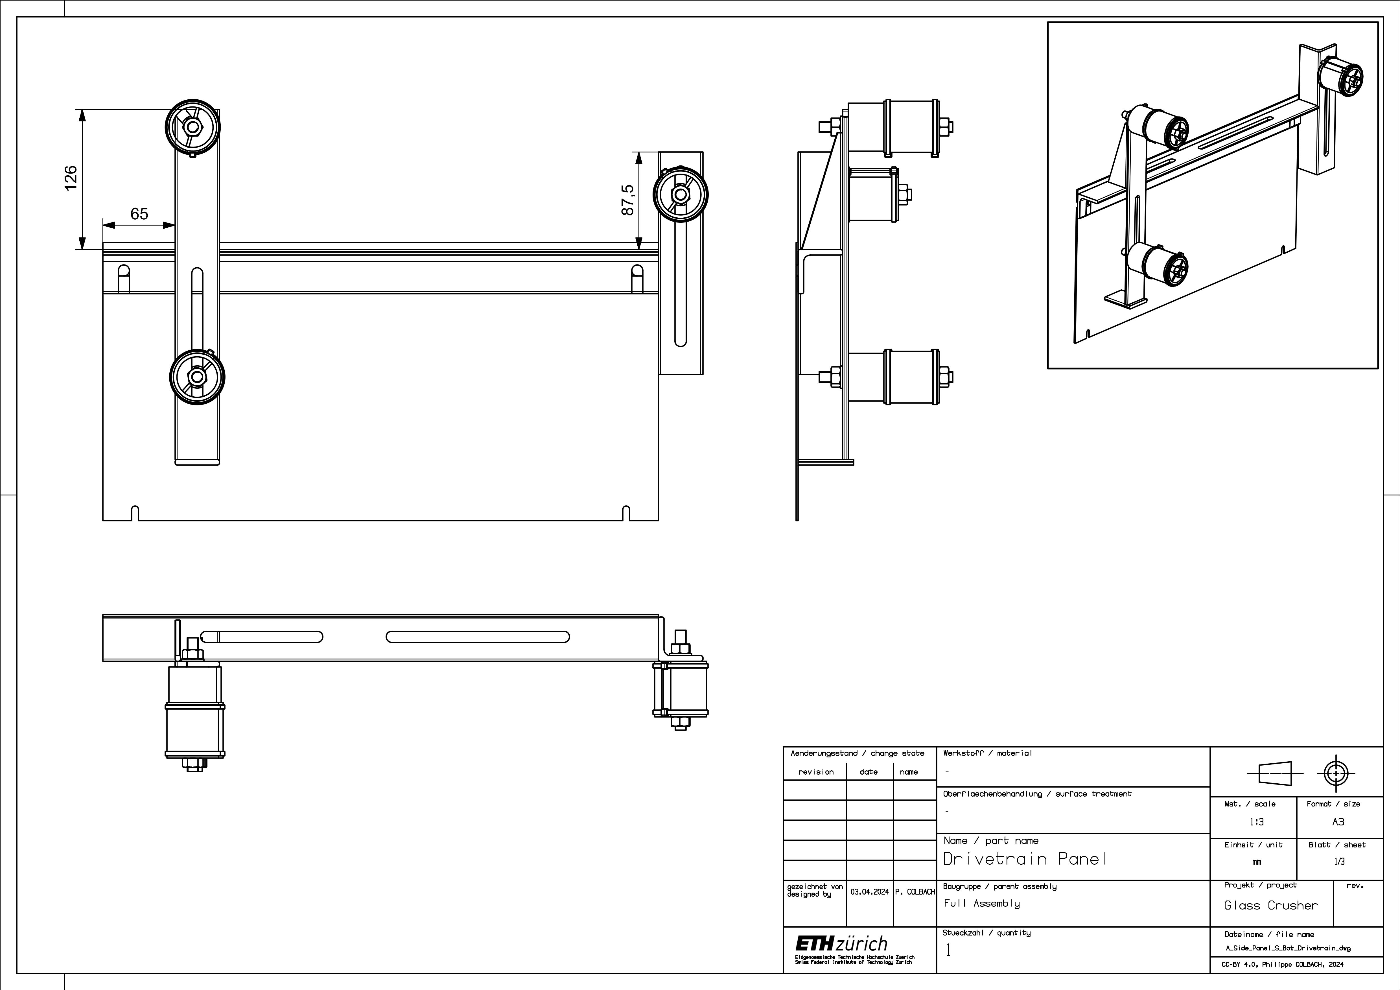
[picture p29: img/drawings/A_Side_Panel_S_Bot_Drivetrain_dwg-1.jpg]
Figure 12: Drive train assembly.


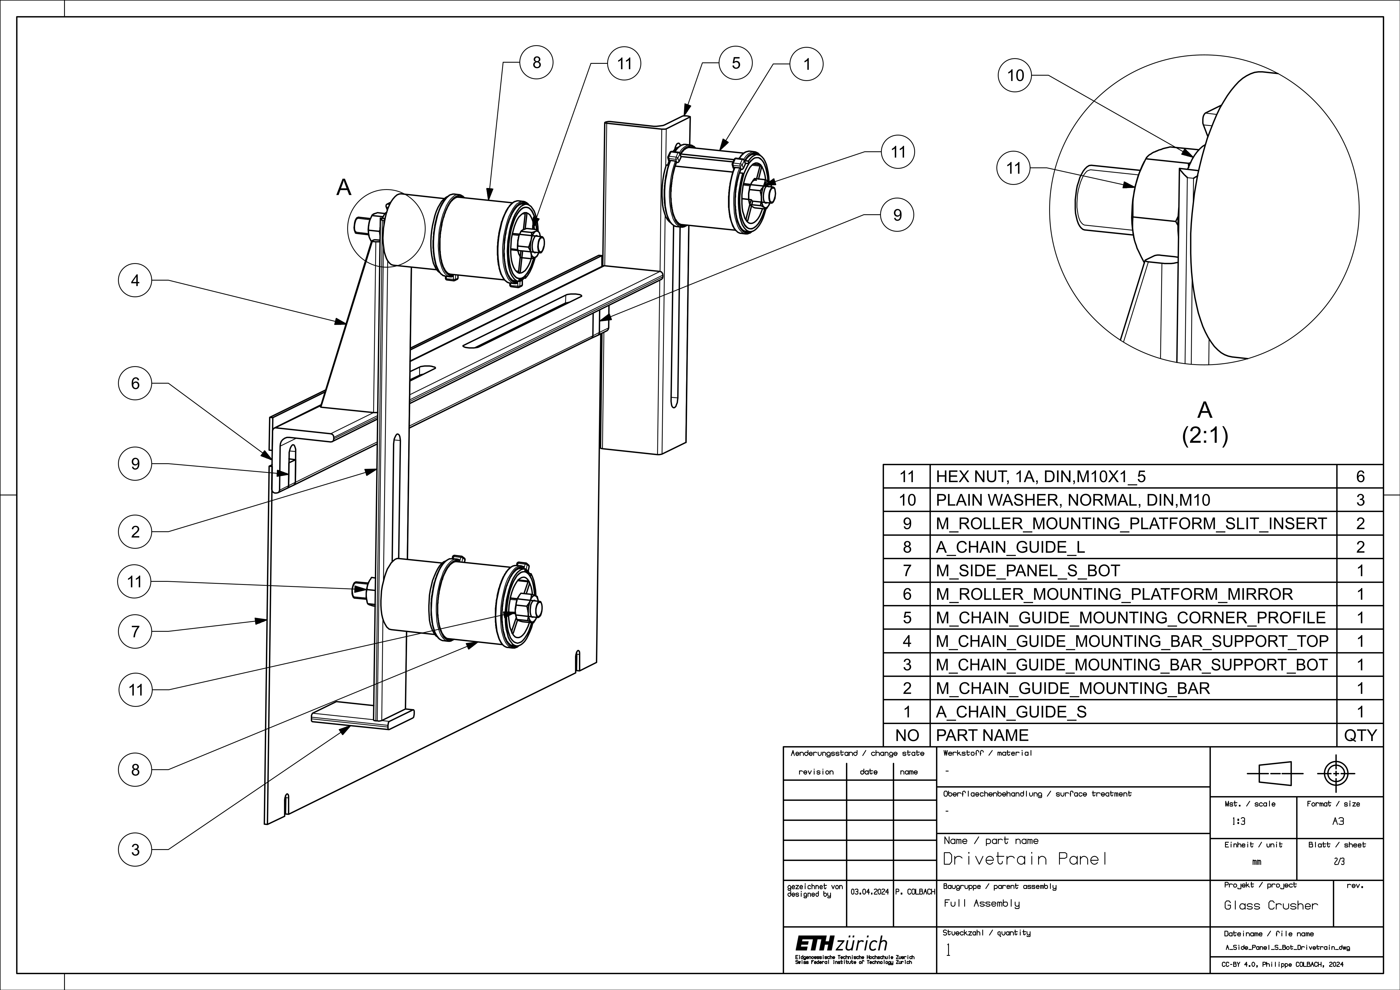
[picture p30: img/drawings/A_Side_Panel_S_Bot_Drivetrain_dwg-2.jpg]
Figure 13: Drive train part list.


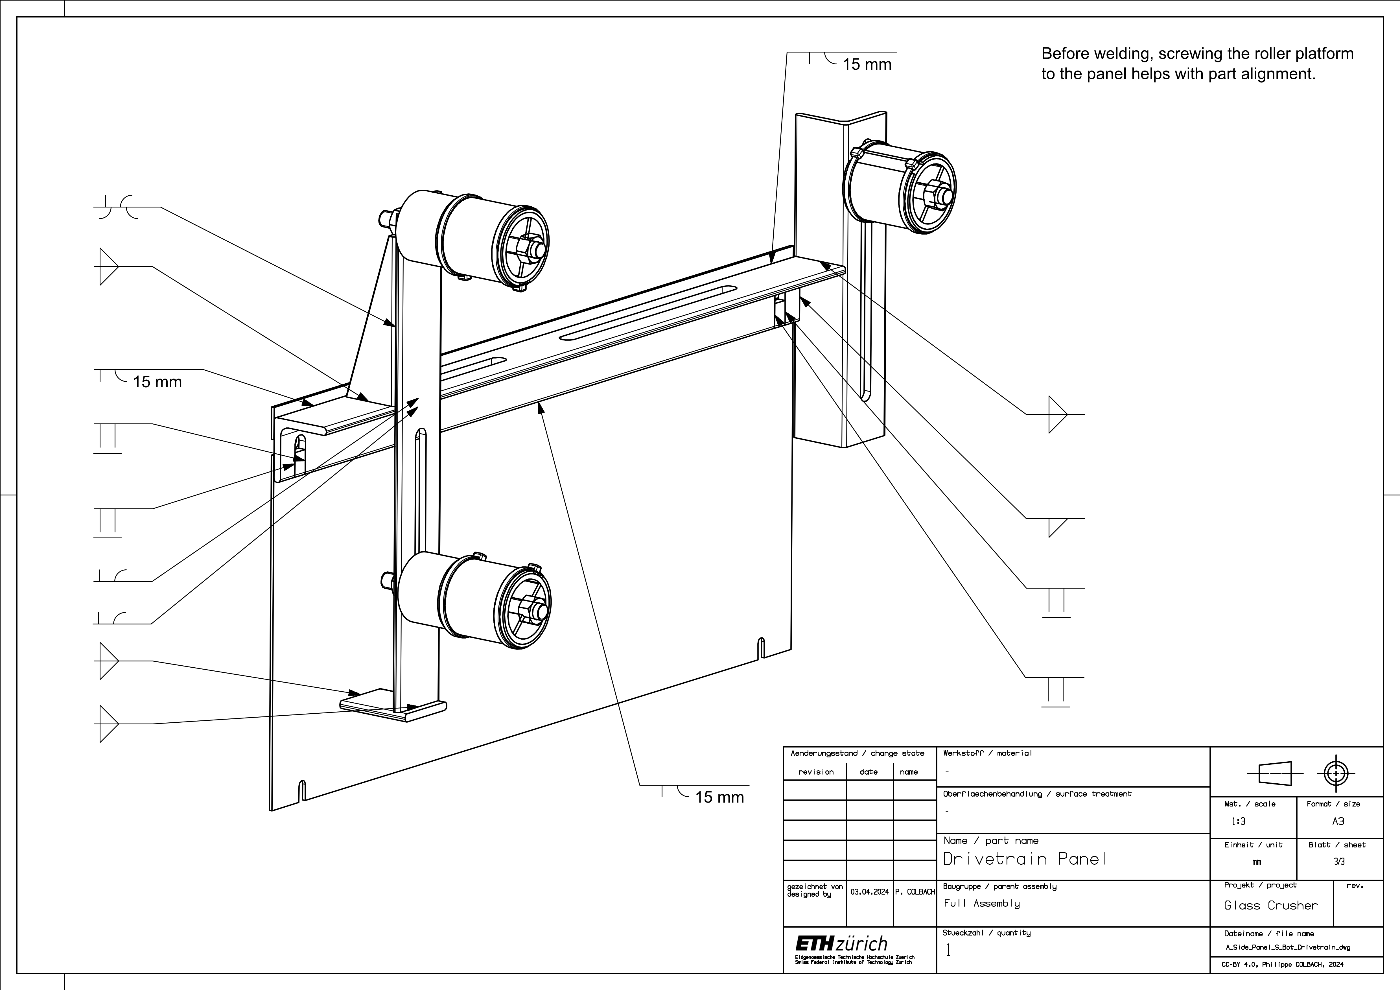
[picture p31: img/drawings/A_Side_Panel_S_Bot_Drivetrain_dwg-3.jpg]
Figure 14: Welding instructions for the drive train assembly.


## Roller Mounting Platform {#sec-roller-platform}

Weld the two inserts (2) to the roller platform (1) and flatten the welds - numbered parts shown in Figure 15.

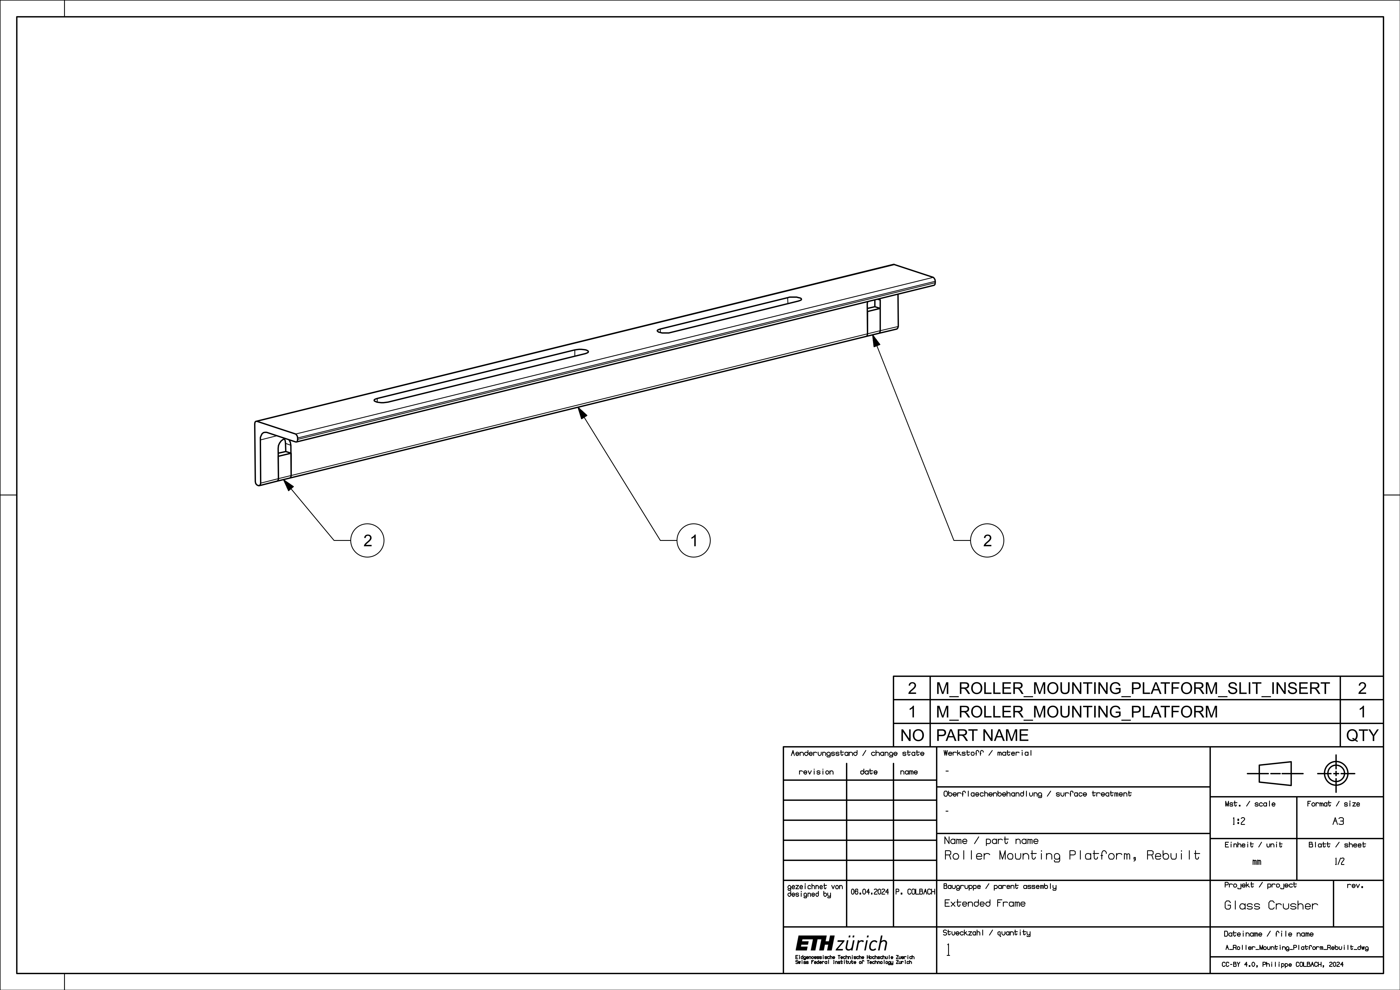
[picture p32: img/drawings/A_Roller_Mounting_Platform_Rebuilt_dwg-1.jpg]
Figure 15: Part list of the roller mounting platform.


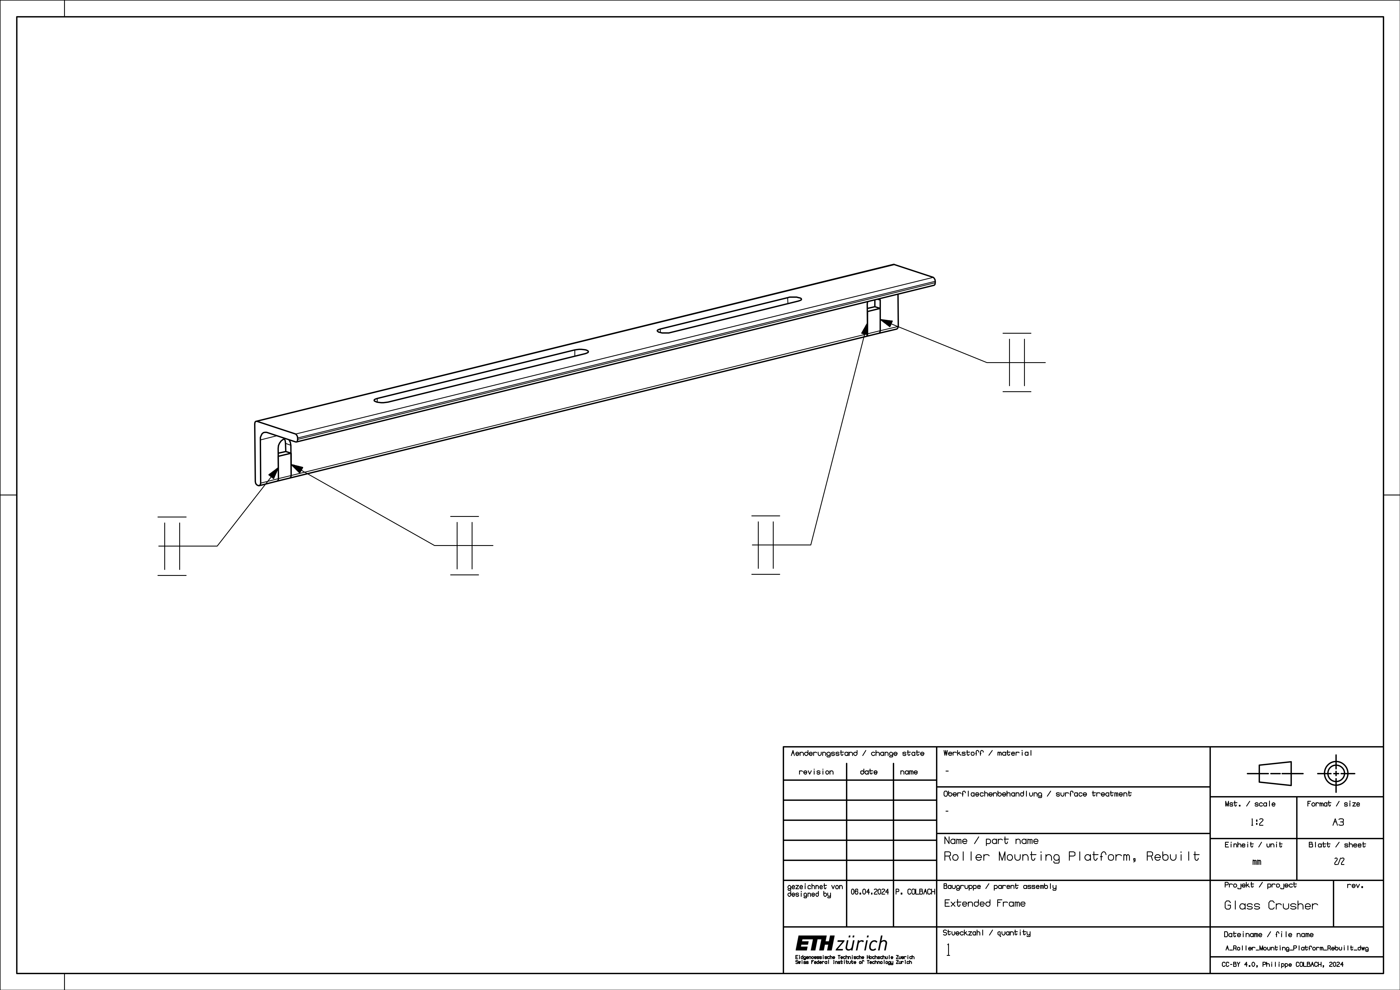
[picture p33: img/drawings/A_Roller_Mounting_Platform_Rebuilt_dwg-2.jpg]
Figure 16: Welding instructions for the roller mounting platform assembly.


## Roller Bearing Brackets {#sec-roller-brackets}

The construction procedure is identical for both the movable and fixed brackets. Start by welding the bracket’s side pieces (7) to the base (1) - numbered parts shown in Figure 18. Add the backplate (4) and use the clamping plate (3) to hold the bearing (2) in place.

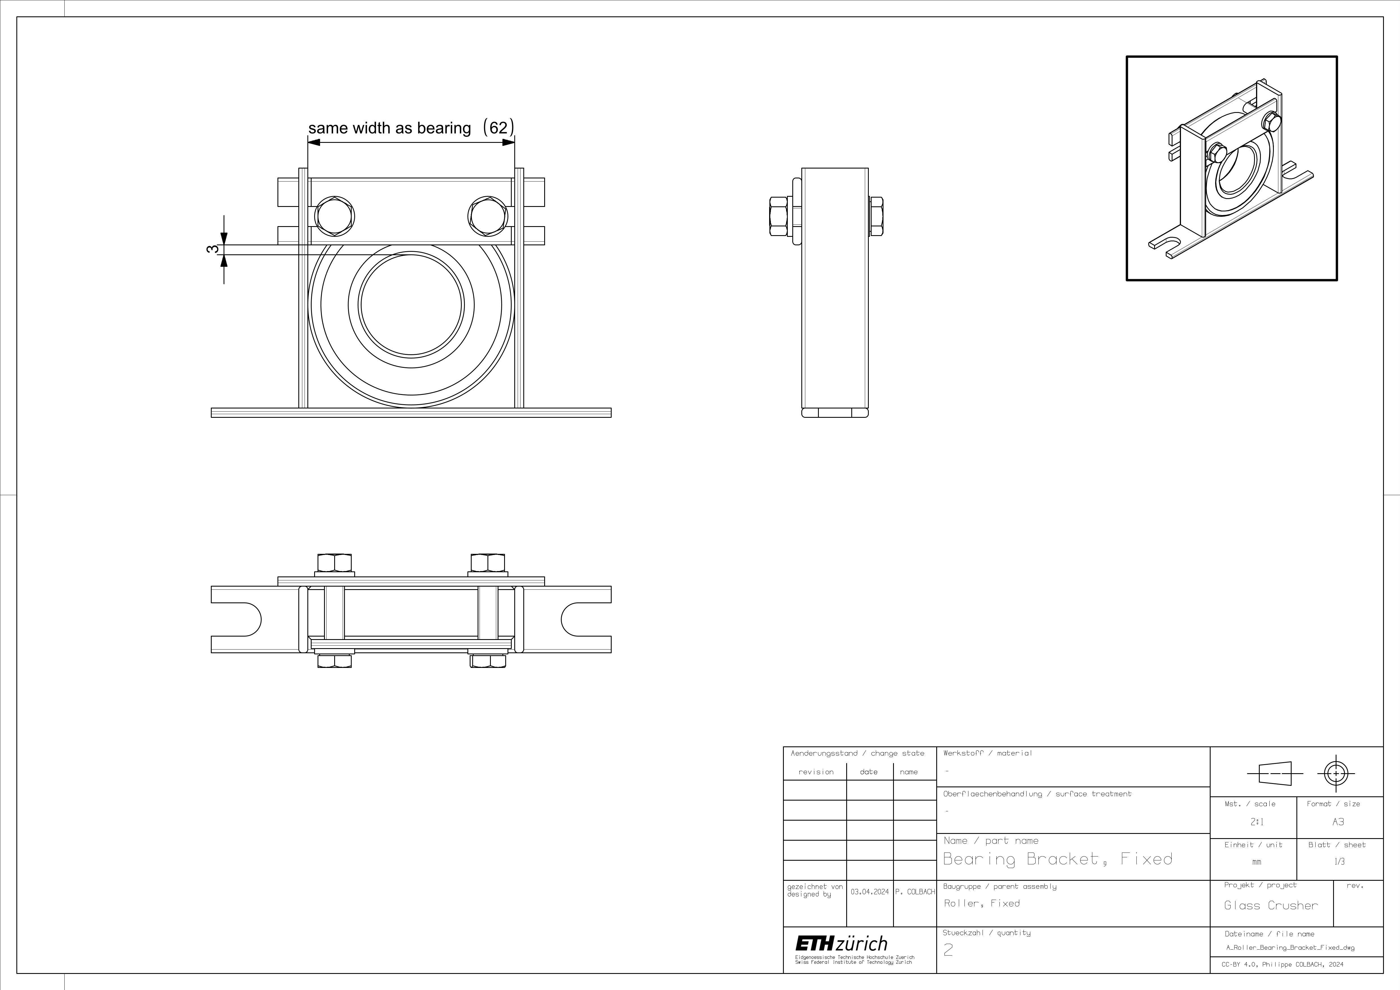
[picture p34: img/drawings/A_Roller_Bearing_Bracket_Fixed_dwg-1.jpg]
Figure 17: Roller bearing bracket assembly.


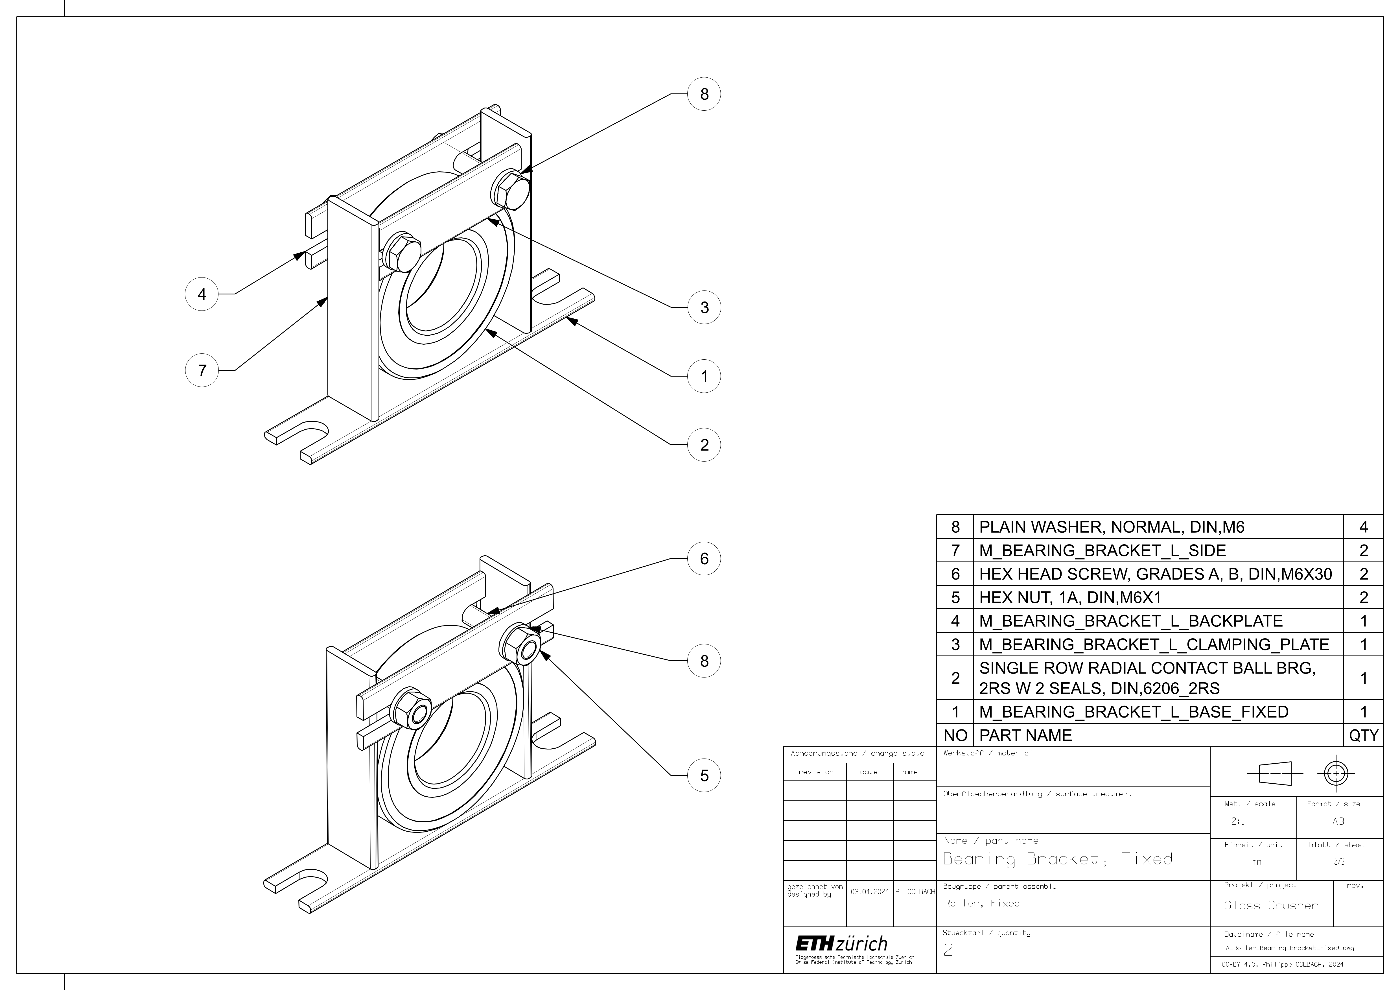
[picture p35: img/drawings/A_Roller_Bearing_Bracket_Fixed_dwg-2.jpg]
Figure 18: Part list of the roller bearing bracket.


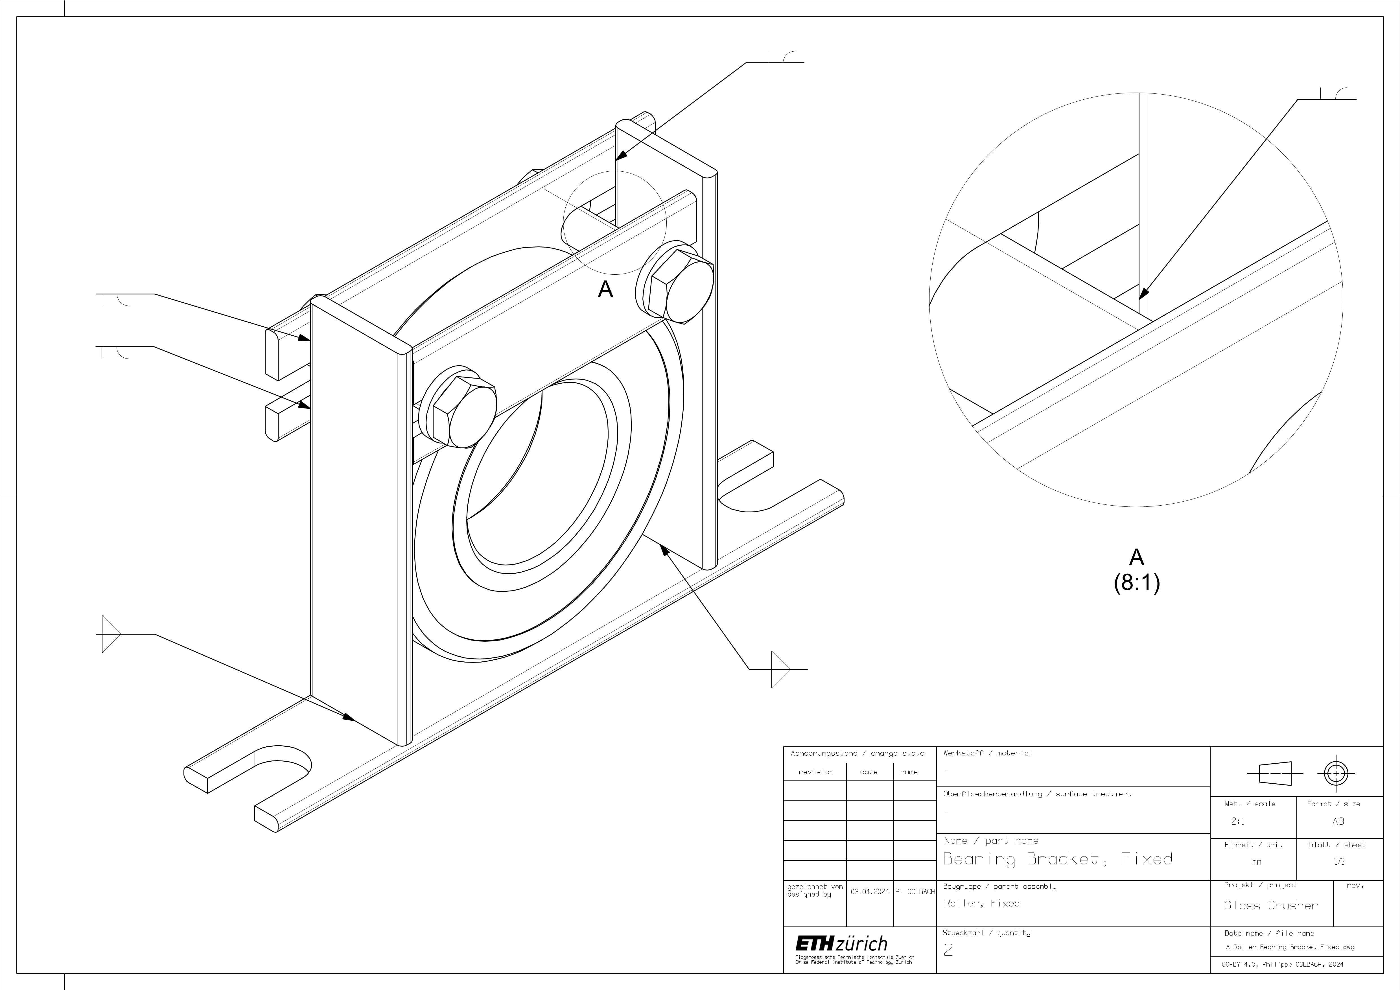
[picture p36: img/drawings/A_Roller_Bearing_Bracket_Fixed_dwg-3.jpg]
Figure 19: Welding instructions for the roller bearing bracket assembly.


## Rollers {#sec-rollers}

Weld the ten square profiles (3) to the roller body (1) - numbered parts shown in Figure 21. Make sure to keep an even spacing between the profiles to avoid collisions during operation. The last step consists of adding the bearing brackets (2) to the roller.

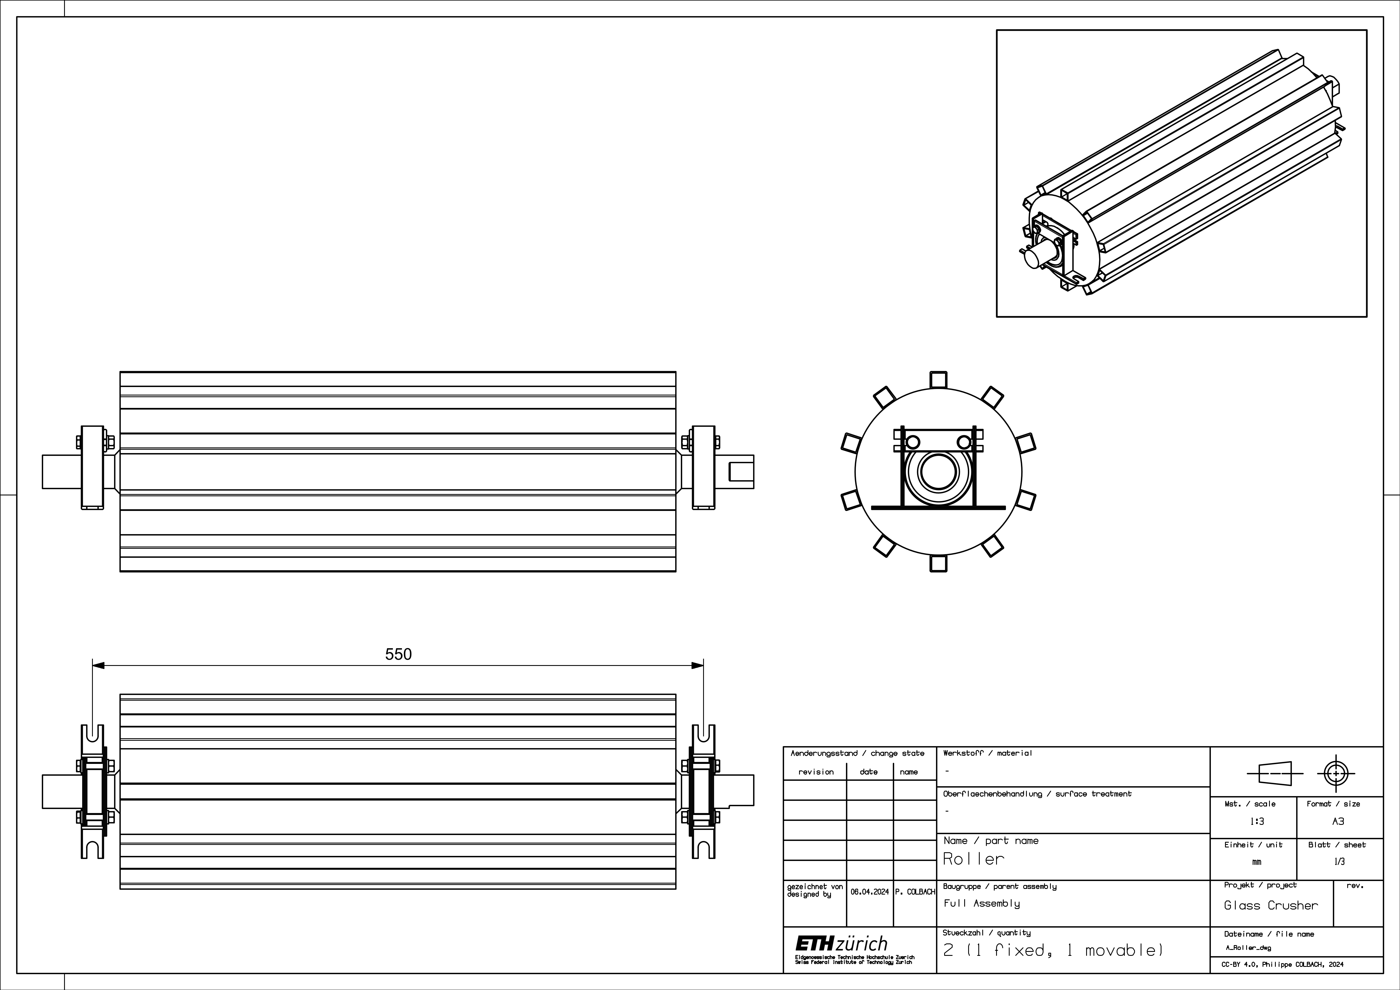
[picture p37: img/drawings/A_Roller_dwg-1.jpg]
Figure 20: Roller assembly.


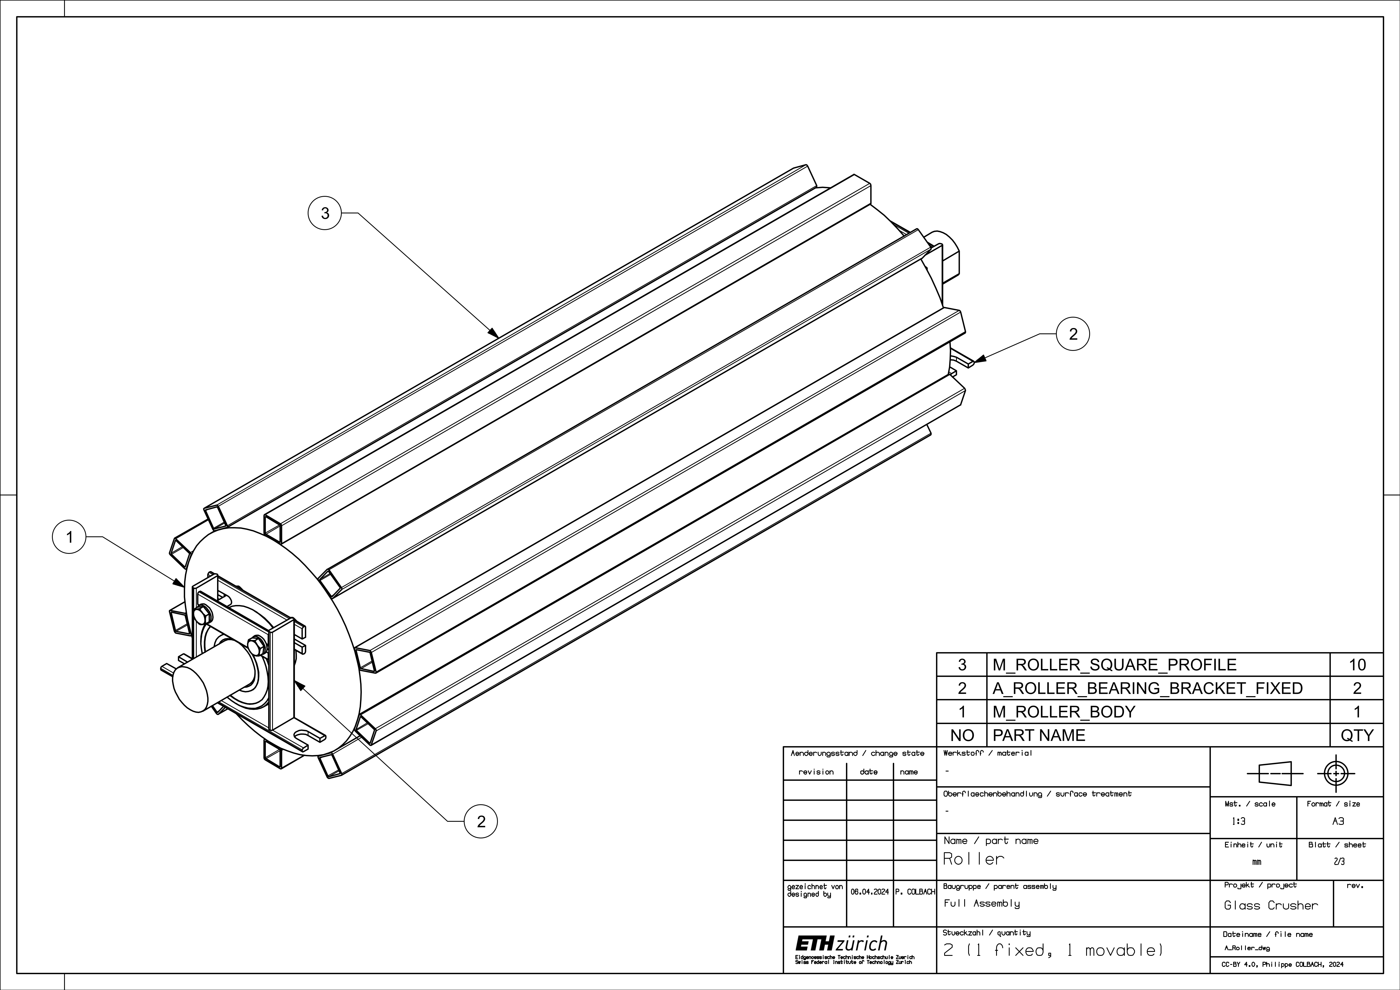
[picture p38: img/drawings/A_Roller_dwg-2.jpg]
Figure 21: Part list of the roller assembly.


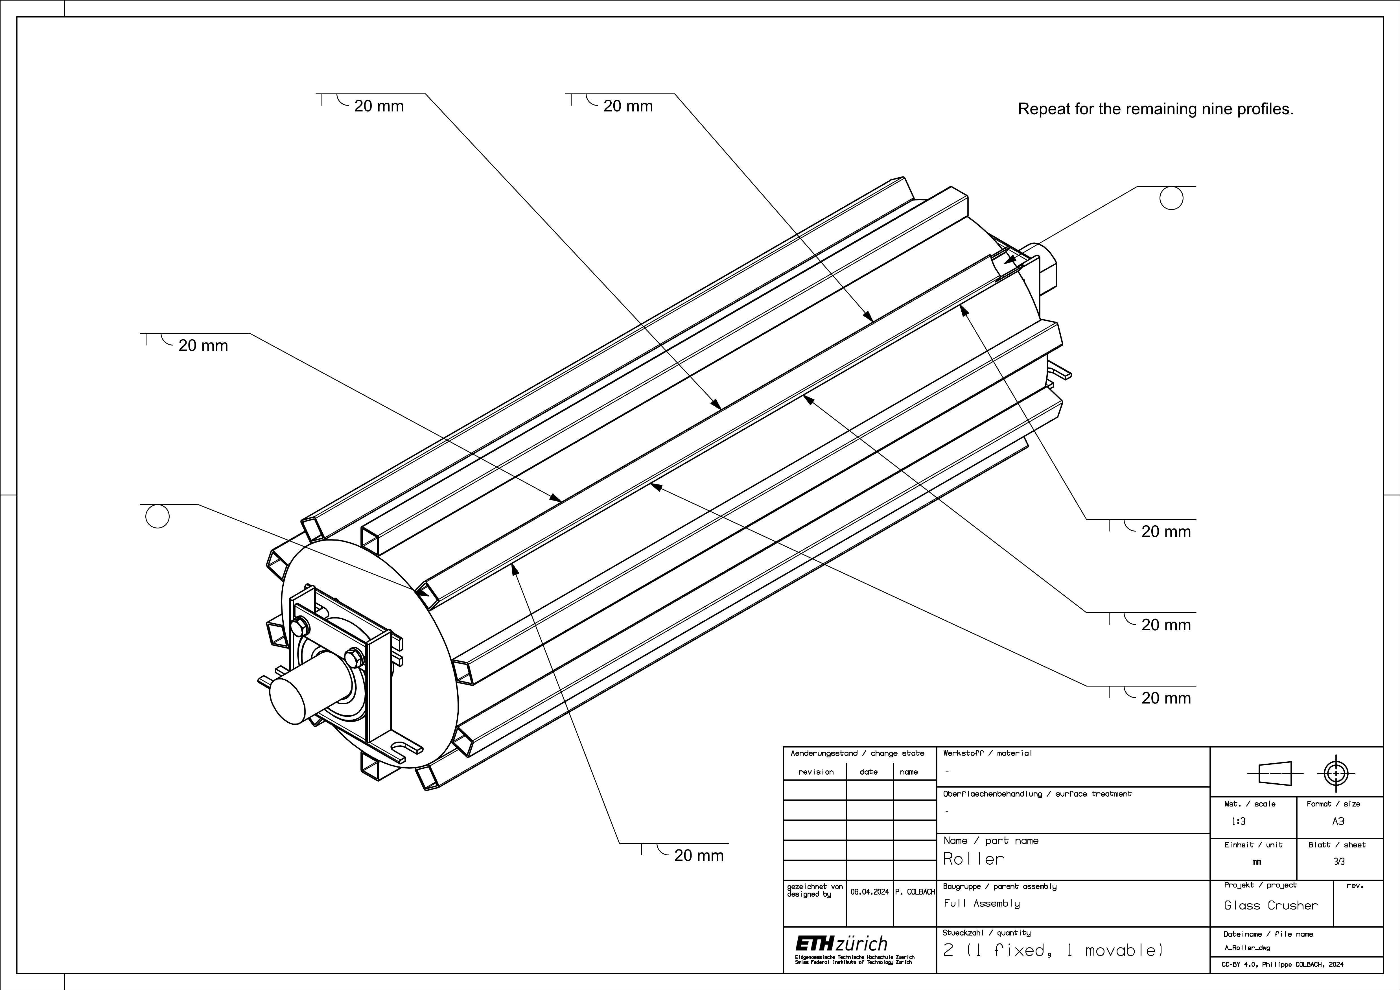
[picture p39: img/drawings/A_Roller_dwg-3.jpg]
Figure 22: Welding instructions for the roller assembly.


## Sprocket Module (Large) {#sec-large-sprocket}

Weld the plate fixations (5) to the backplate (3) - numbered parts shown in Figure 24. To ensure a good fit, it is best to only weld one of the fixation pieces at first, then mount the backplate plate onto the shaft using the two screws (4) and the second fixation piece to temporarily hold it in place, and only then weld the second fixation piece to the plate. Remember that the roller shafts have a flat cutout and that the centerline between the plate fixations does not align with the roller’s center of rotation. Next, weld the two screw heads (4) to the plate fixation. Mount the small sprocket (2) on the front plate (1) before attaching everything to the large sprocket (4).

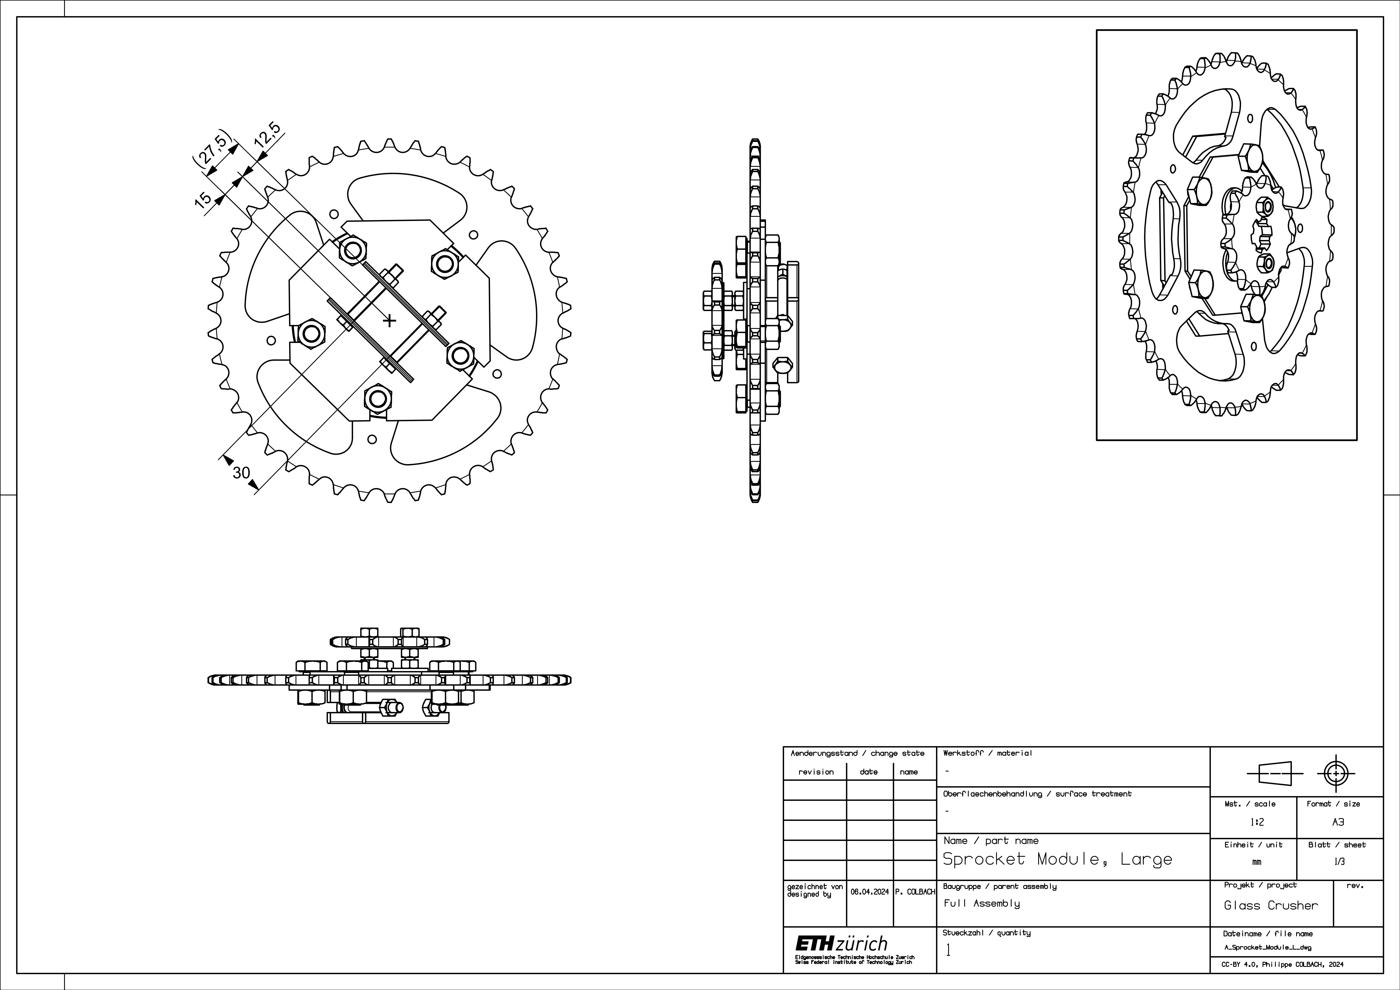
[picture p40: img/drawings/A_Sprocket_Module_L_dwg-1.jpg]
Figure 23: Large sprocket module assembly.


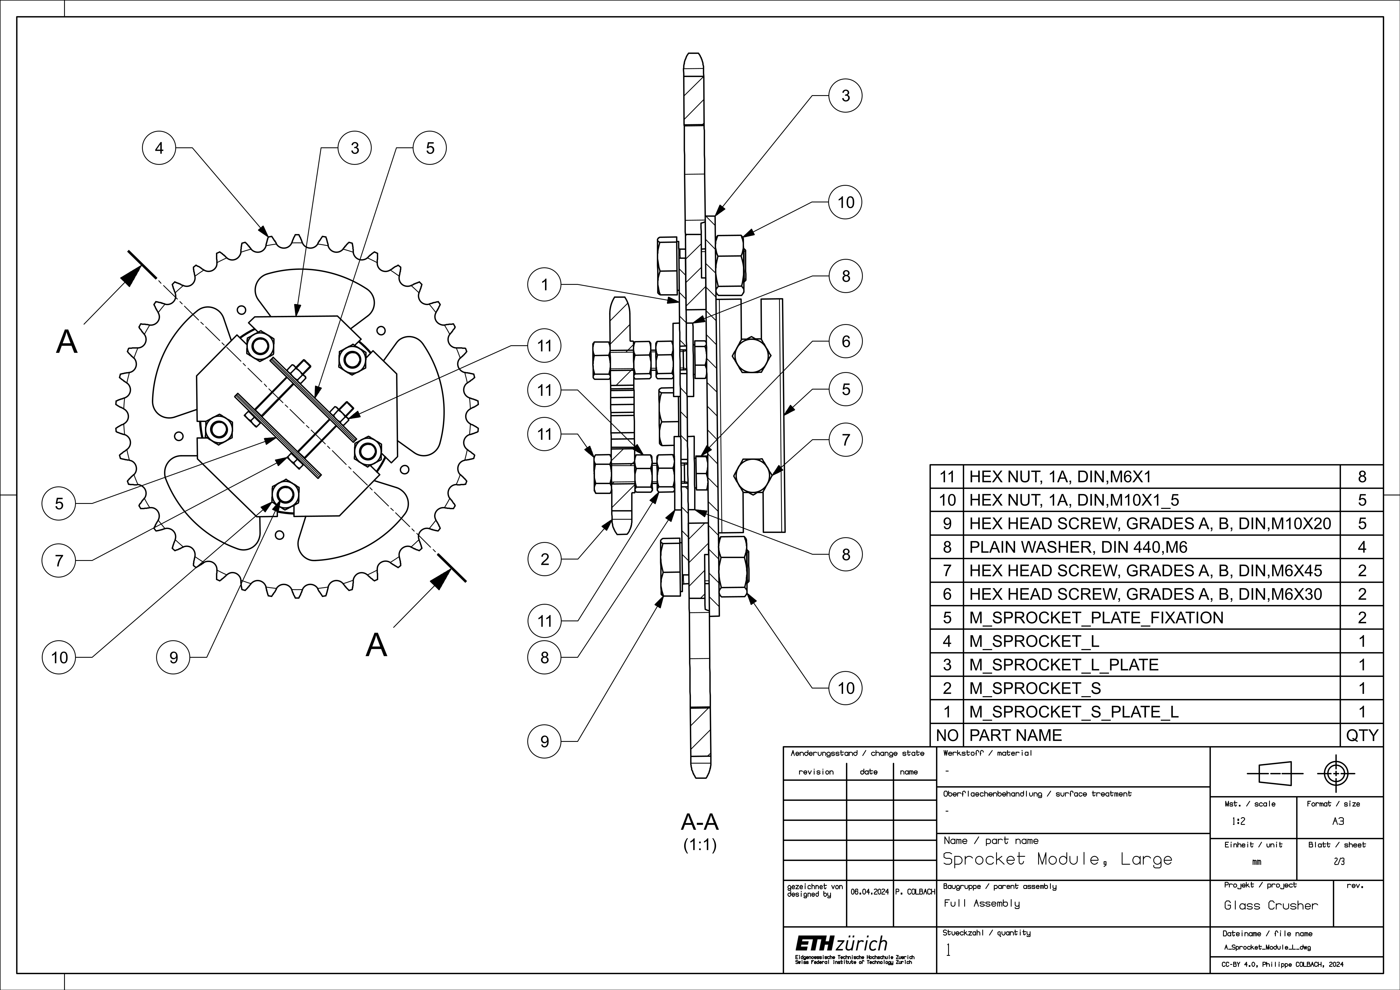
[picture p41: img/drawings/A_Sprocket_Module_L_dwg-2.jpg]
Figure 24: Part list of the large sprocket module.


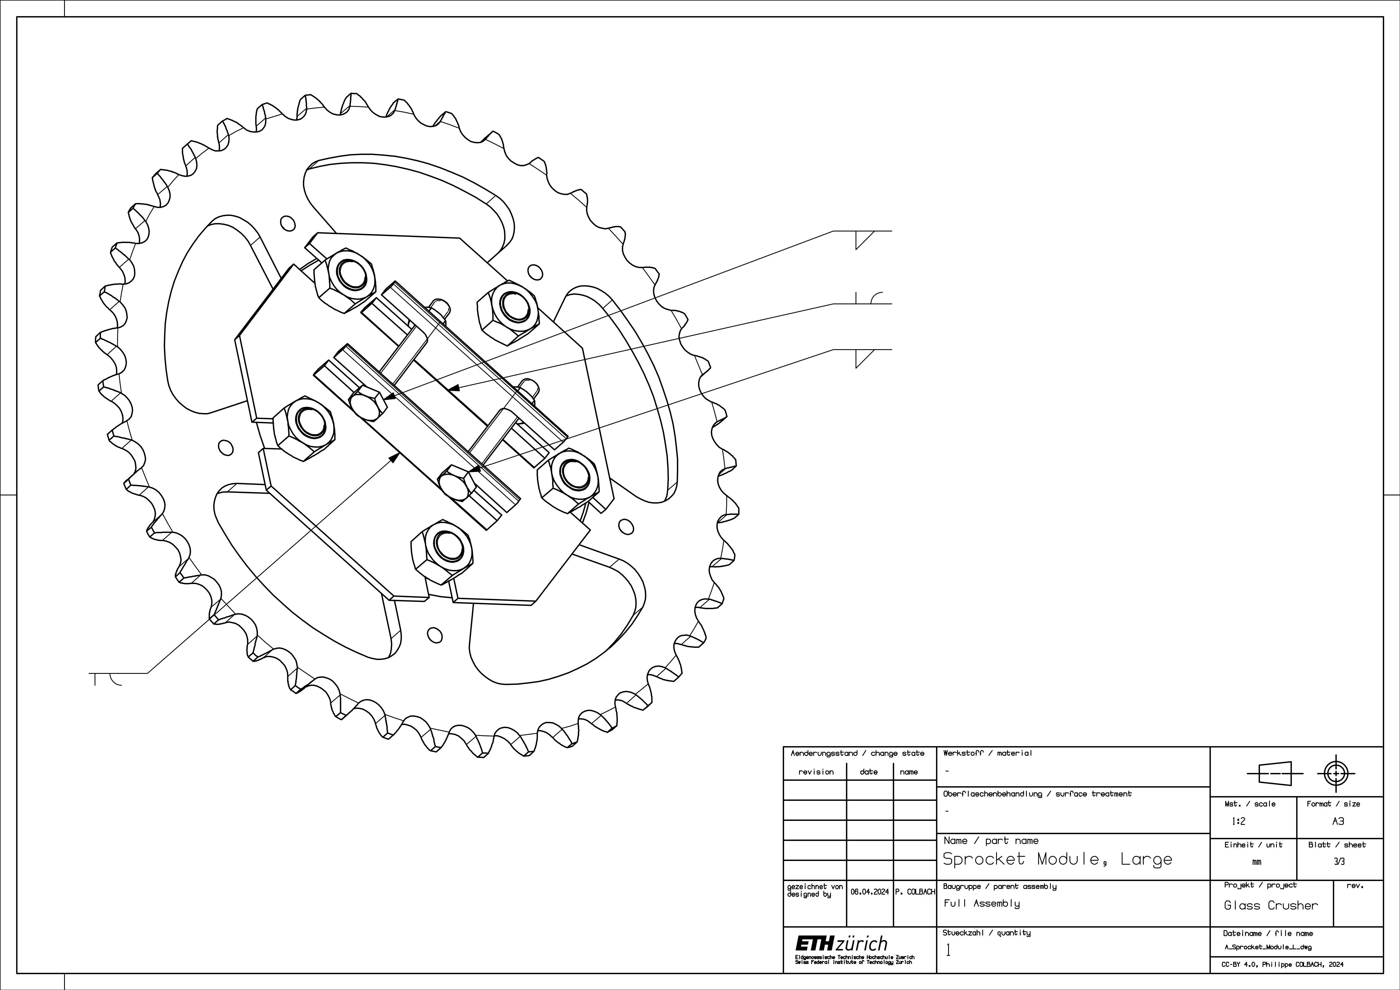
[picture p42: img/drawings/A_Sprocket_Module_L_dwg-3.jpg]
Figure 25: Welding instructions for the large sprocket module.


## Sprocket Module (Small) {#sec-small-sprocket}

Add the plate fixations (6) to the backplate (2), analogously to the large sprocket module - numbered parts shown in Figure 27. Attach the sprocket (3) to the front plate (1), then mount the front plate to the backplate.

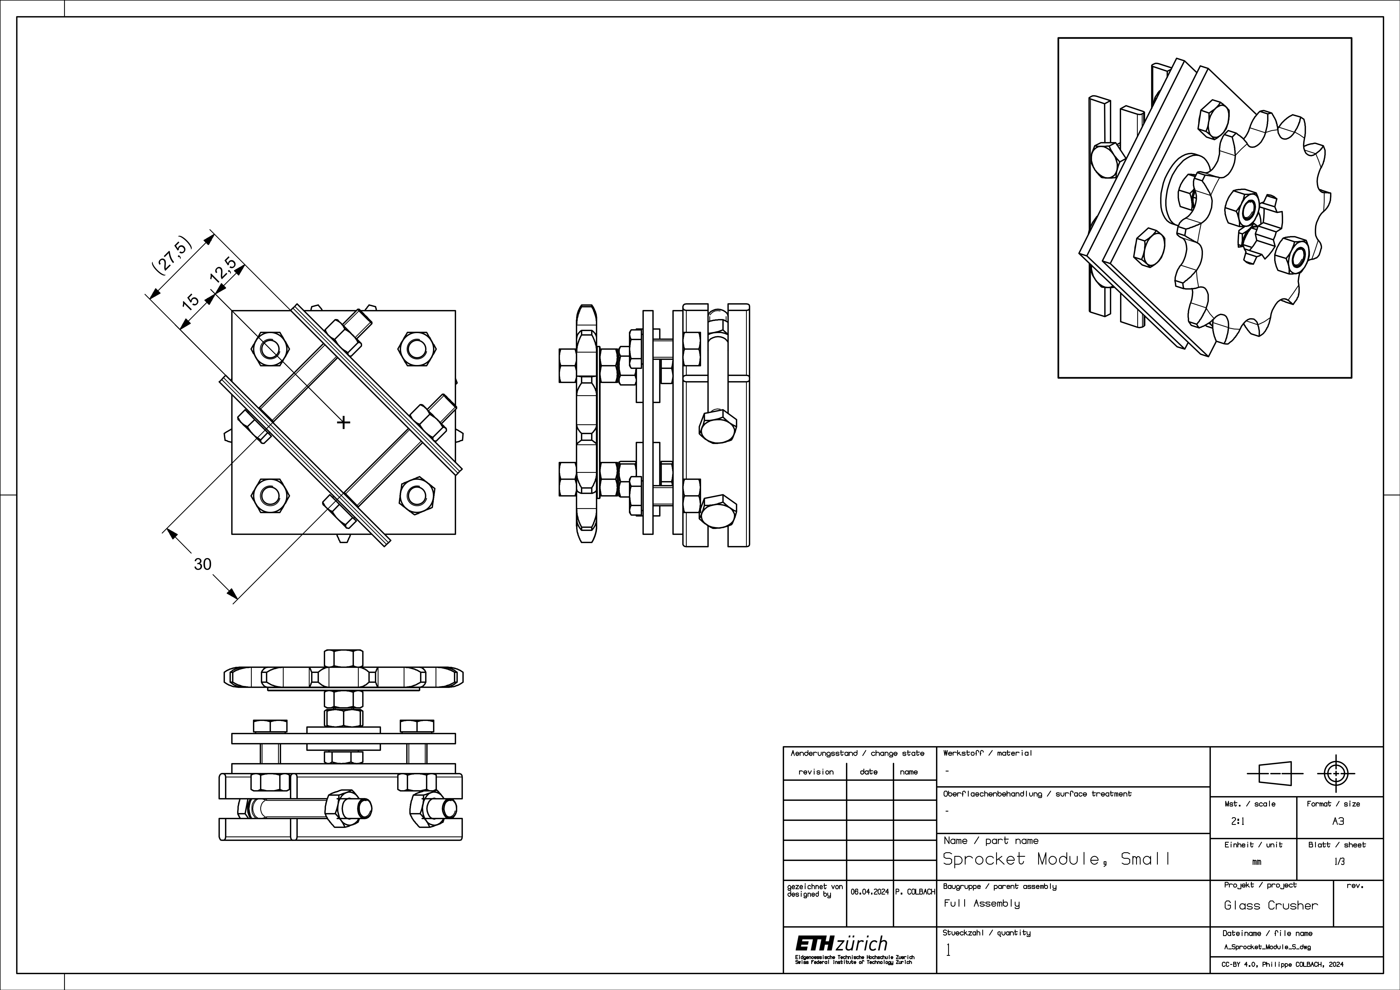
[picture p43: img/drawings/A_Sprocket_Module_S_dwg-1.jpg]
Figure 26: Small sprocket module assembly.


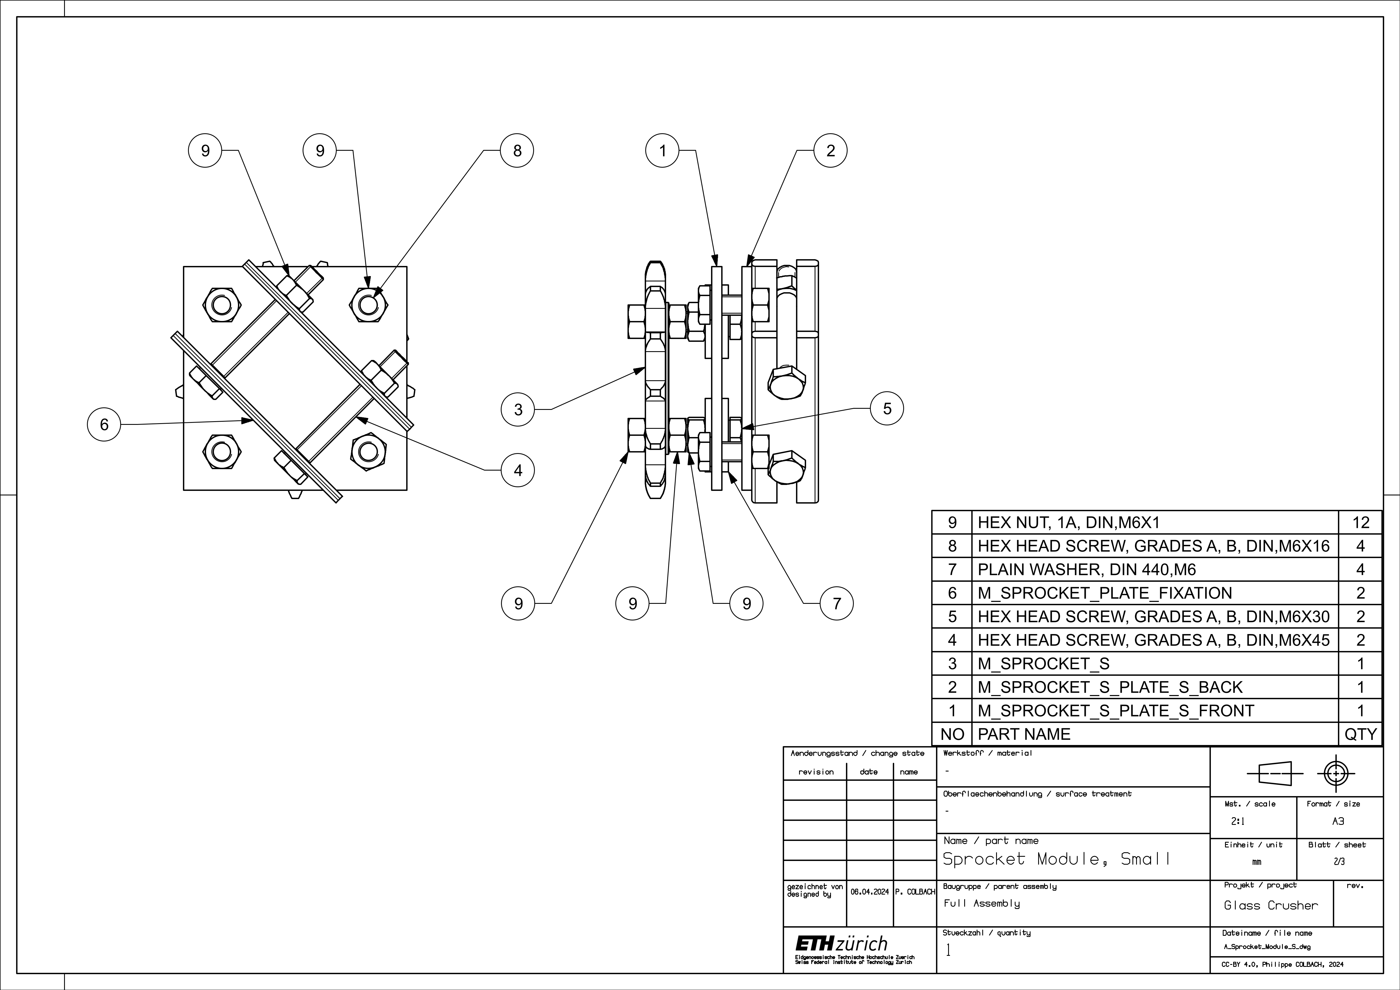
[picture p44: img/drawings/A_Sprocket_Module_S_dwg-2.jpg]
Figure 27: Part list of the small sprocket module.


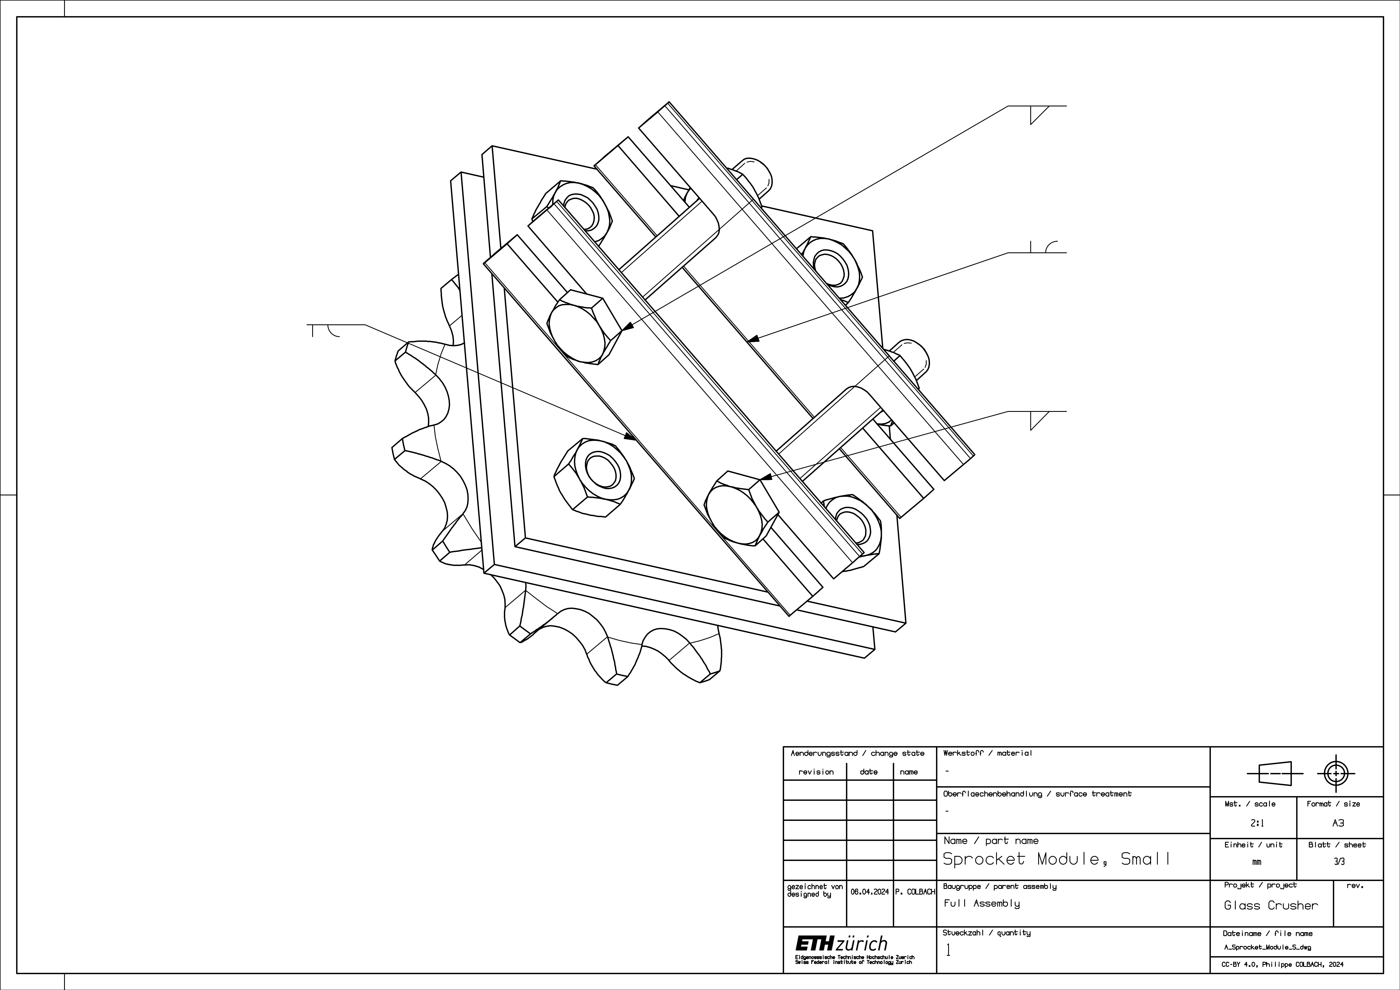
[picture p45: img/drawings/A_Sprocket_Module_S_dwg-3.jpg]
Figure 28: Welding instructions for the small sprocket module.


## Motorcycle Chain {#sec-chain}

If the chain has more than 66 links, it will most likely have to be shortened.

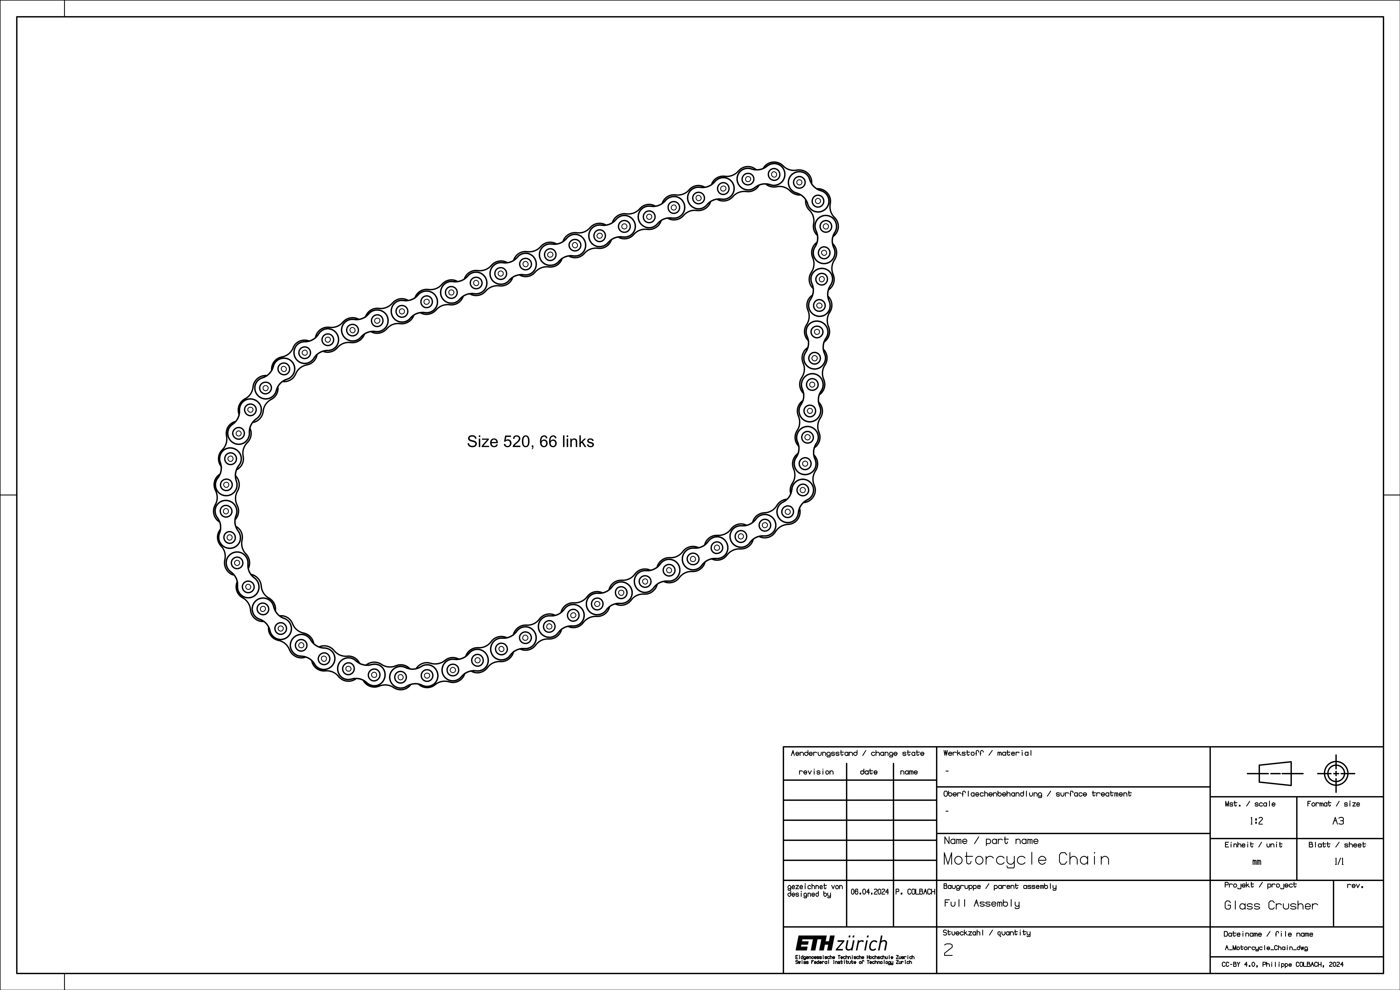
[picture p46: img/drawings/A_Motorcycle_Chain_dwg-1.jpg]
Figure 29: Motorcycle chain.


## Upper Side Panels {#sec-upper-side-panels}

Weld the stud (3) to the panel’s (2) slot - numbered parts shown in Figure 31. The two panels must have their stud on opposite sides to make sure they are both pointing away from the crusher once installed.

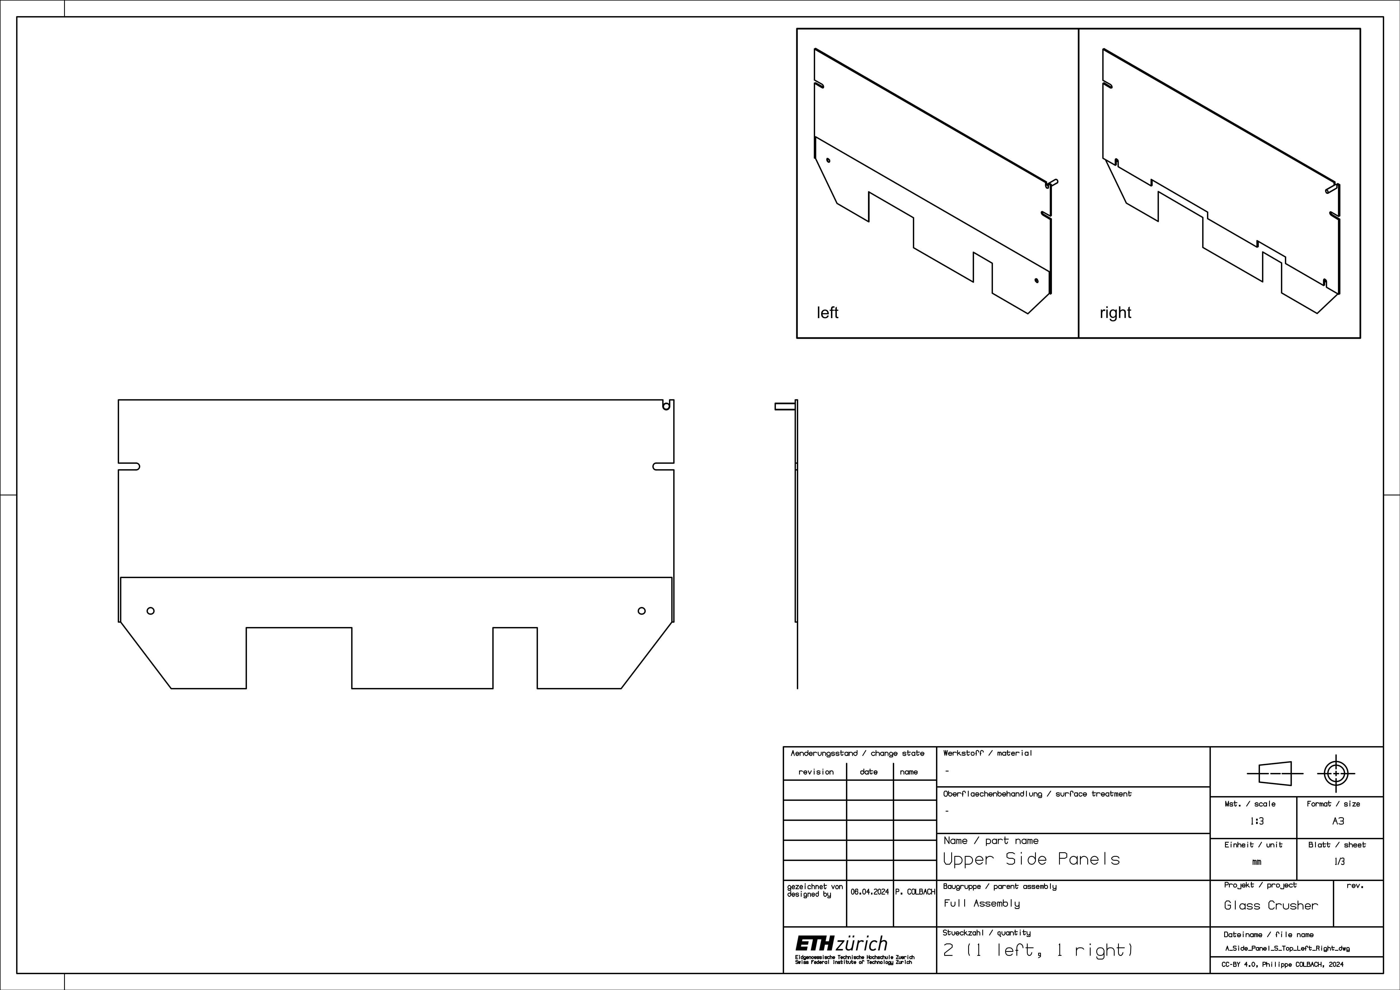
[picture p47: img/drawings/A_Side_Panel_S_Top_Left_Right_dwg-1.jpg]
Figure 30: Upper side panel assembly.


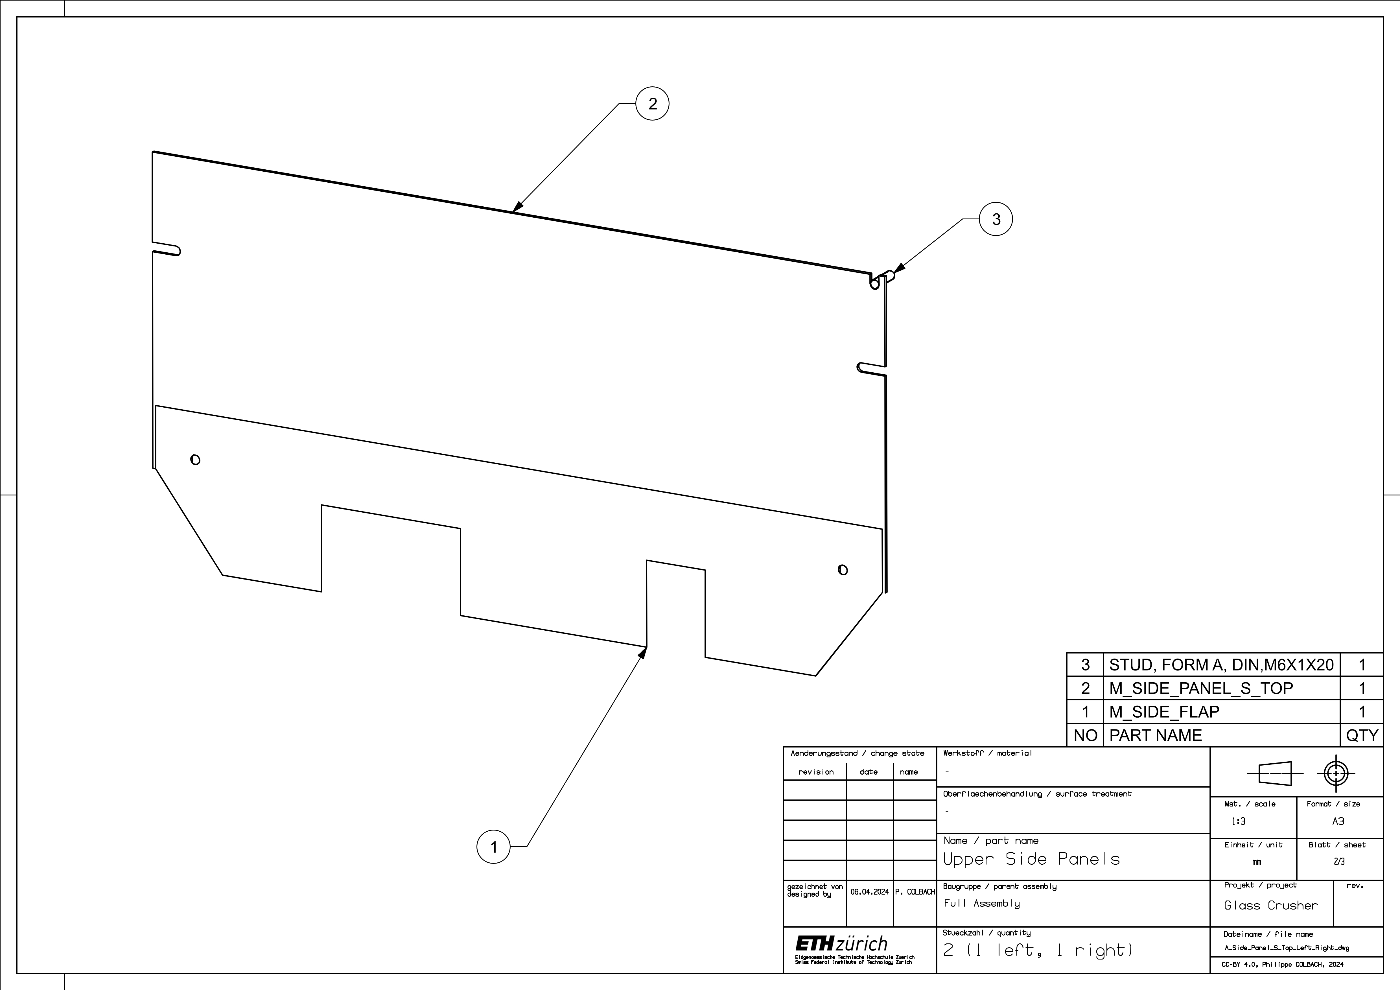
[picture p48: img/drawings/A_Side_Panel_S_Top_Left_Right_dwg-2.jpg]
Figure 31: Upper side panel part list.


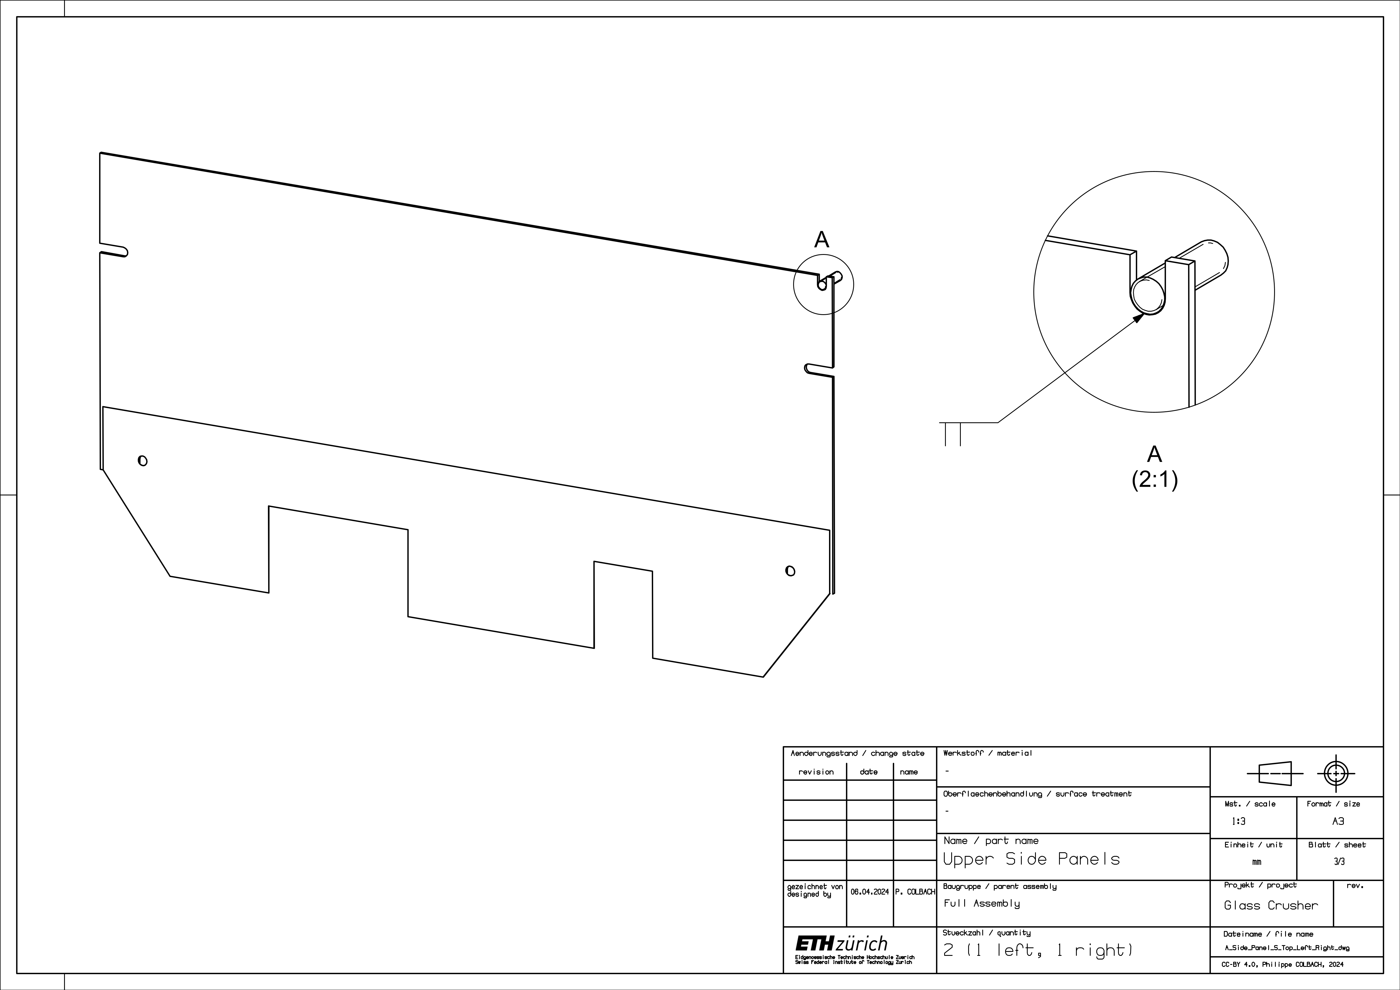
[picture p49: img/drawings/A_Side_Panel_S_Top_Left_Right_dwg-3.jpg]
Figure 32: Welding instructions for the upper side panel assembly.


## Cover {#sec-cover}

To make sure the cover fits the way it should, it is recommended to build the cover directly on top of the crusher. To do so, proceed as follows. First, attach the upper side panels, the crank side panel and the large side panel to the frame. Mark the position of the large funnel plate (5) on the inside of the crusher’s upper side panels - numbered part list shown in Figure 34. Make sure the panel is aligned with the marking, then weld the funnel support (2) to it. Next, mark the position of the smaller funnel panel (6) on the inside of the upper side panels. Place both the larger and smaller funnel panel into the crusher, make sure they are aligned with their marking, then weld the side panels (9) to them. Add the chute plate (7) and its side pieces (12). If it did not already do so before, the cover structure should be able to maintain its position on its own by now. With the cover structure still inside the crusher, place the cover supports (3) & (8) onto their respective pin on the upper side panels. Make sure they are vertically aligned, then weld them to the chute’s side pieces (12) and subsequently add the chute supports (11), the crossbar (4), and the two struts (10). Finally, attach the soft cover (1) and the front flaps (13) using zip ties (14) & (15).

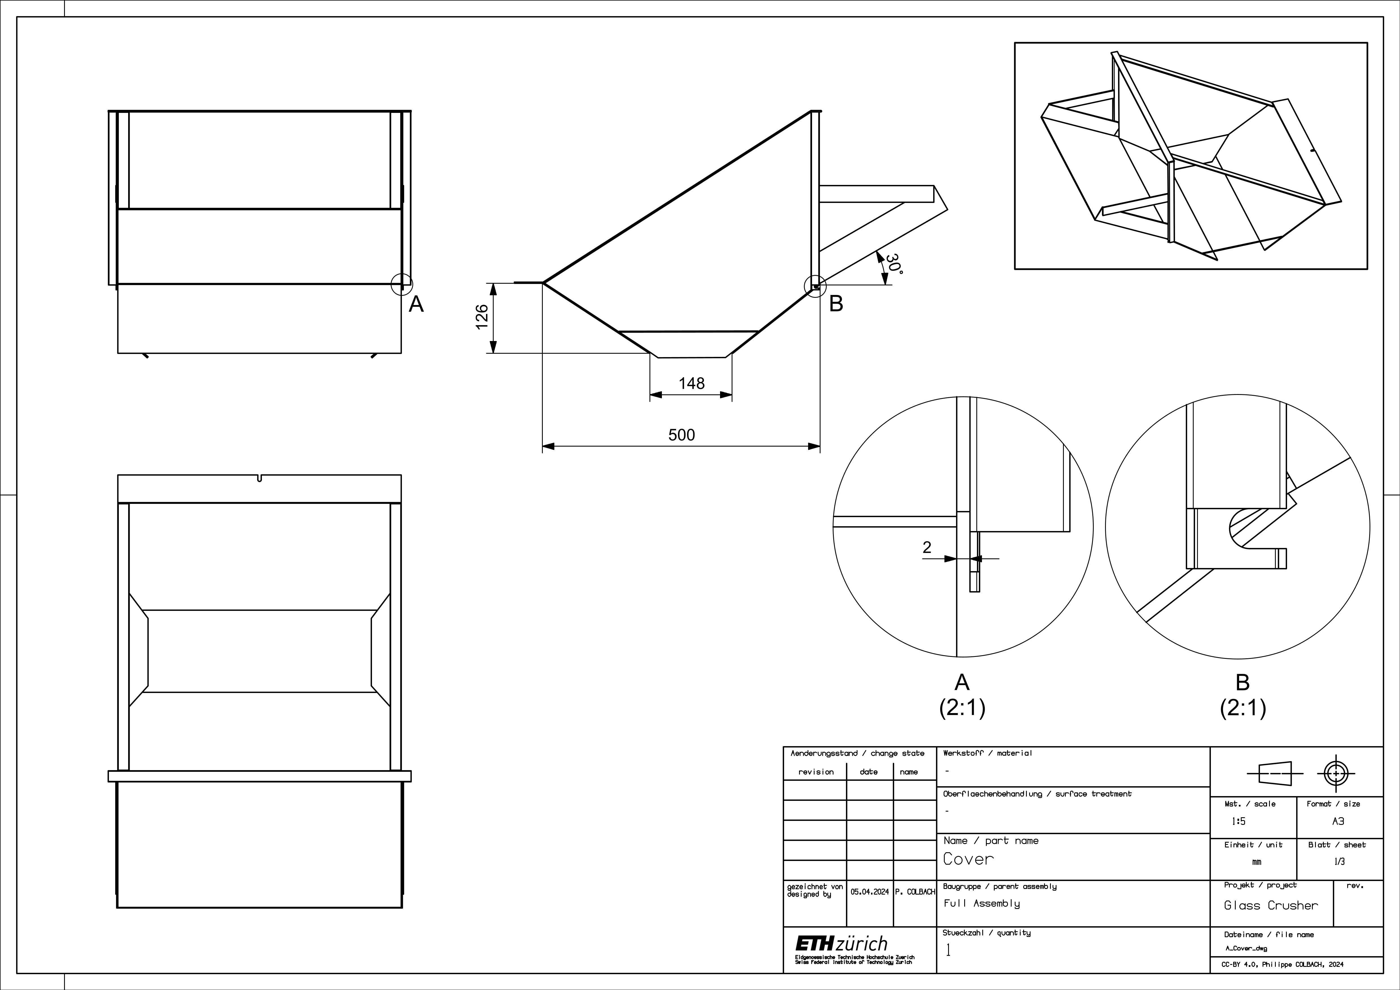
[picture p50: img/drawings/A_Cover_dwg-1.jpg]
Figure 33: Cover assembly.


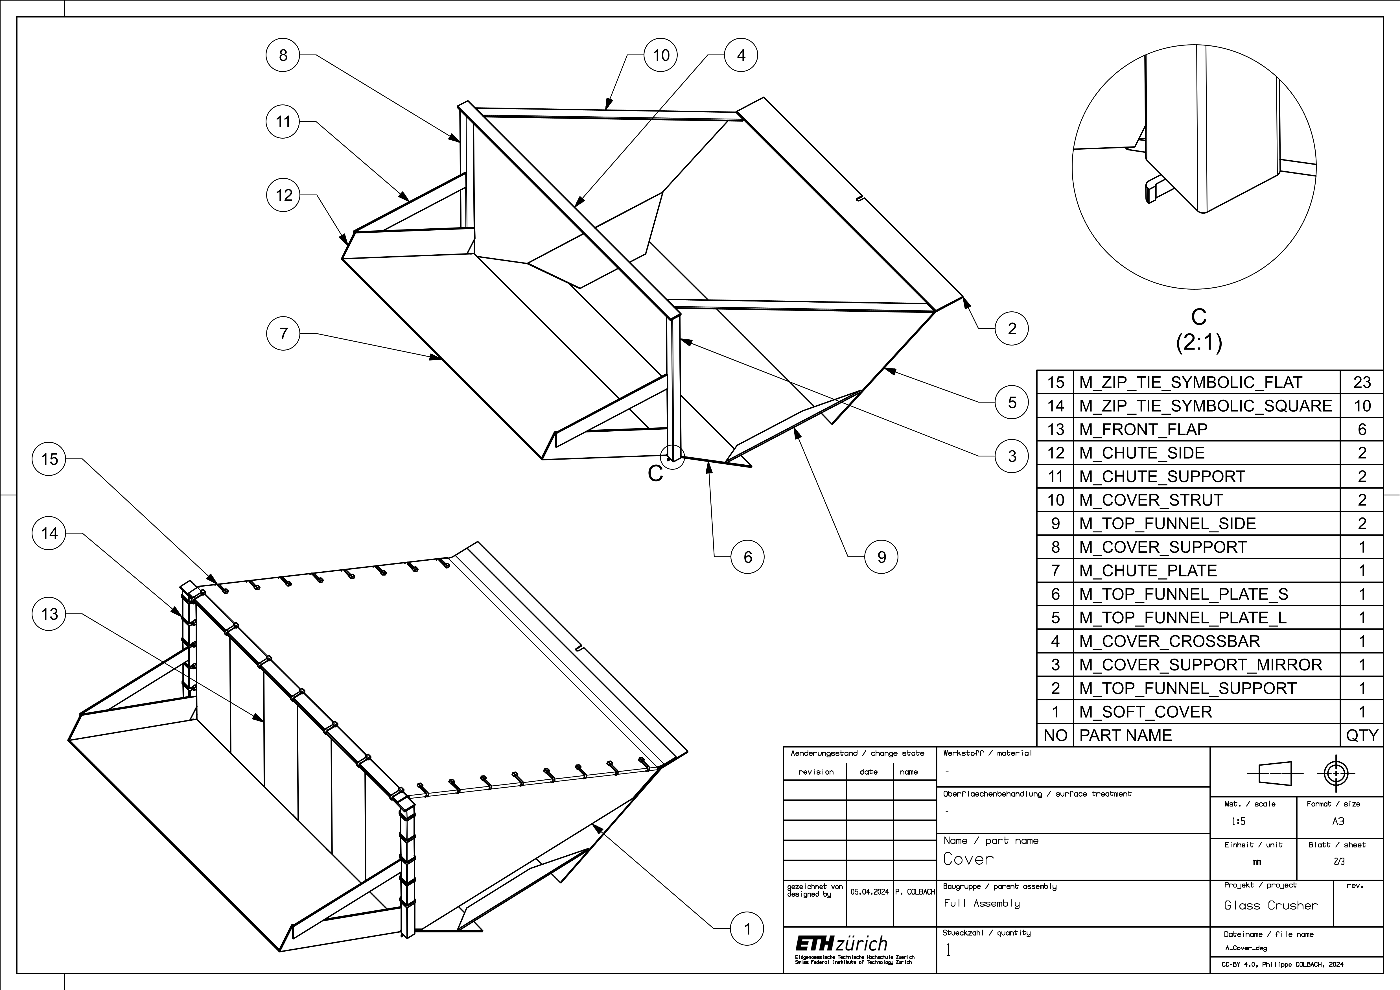
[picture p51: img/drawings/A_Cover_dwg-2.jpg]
Figure 34: Cover part list.


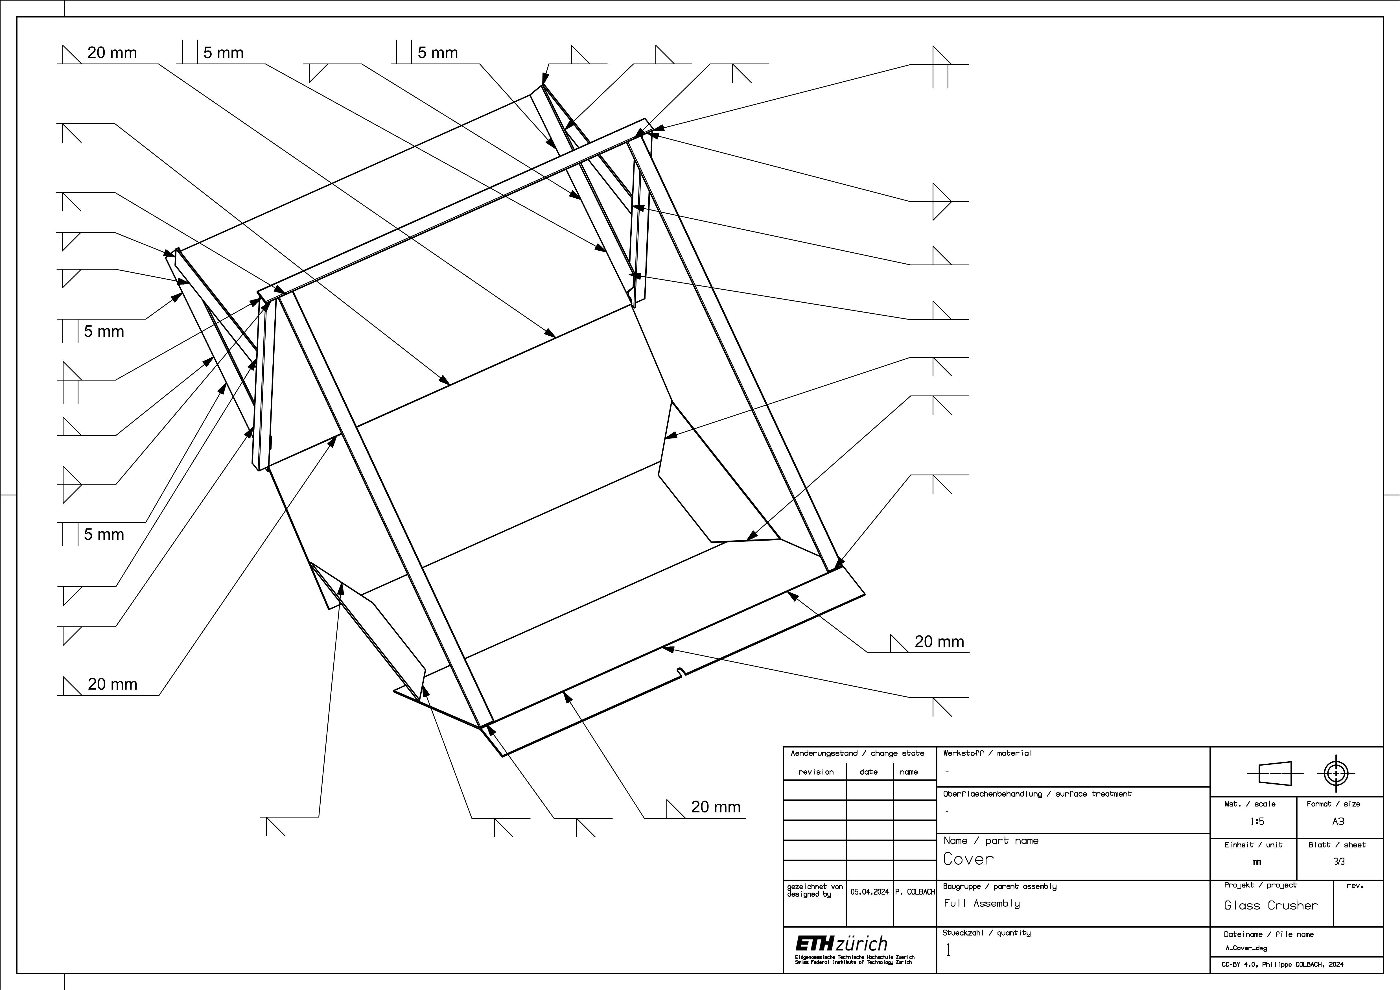
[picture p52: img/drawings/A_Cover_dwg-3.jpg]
Figure 35: Welding instructions for the cover.


# Full Assembly {#sec-full-assembly}

The recommended assembly order goes as follows. First, attach the large side panel (4), the crank side panel (6) with the crank (2), the drivetrain panel (5), the lower side panel (3), and the roller mounting platform (1) to the frame (7) - numbered part list shown in Figure 36.

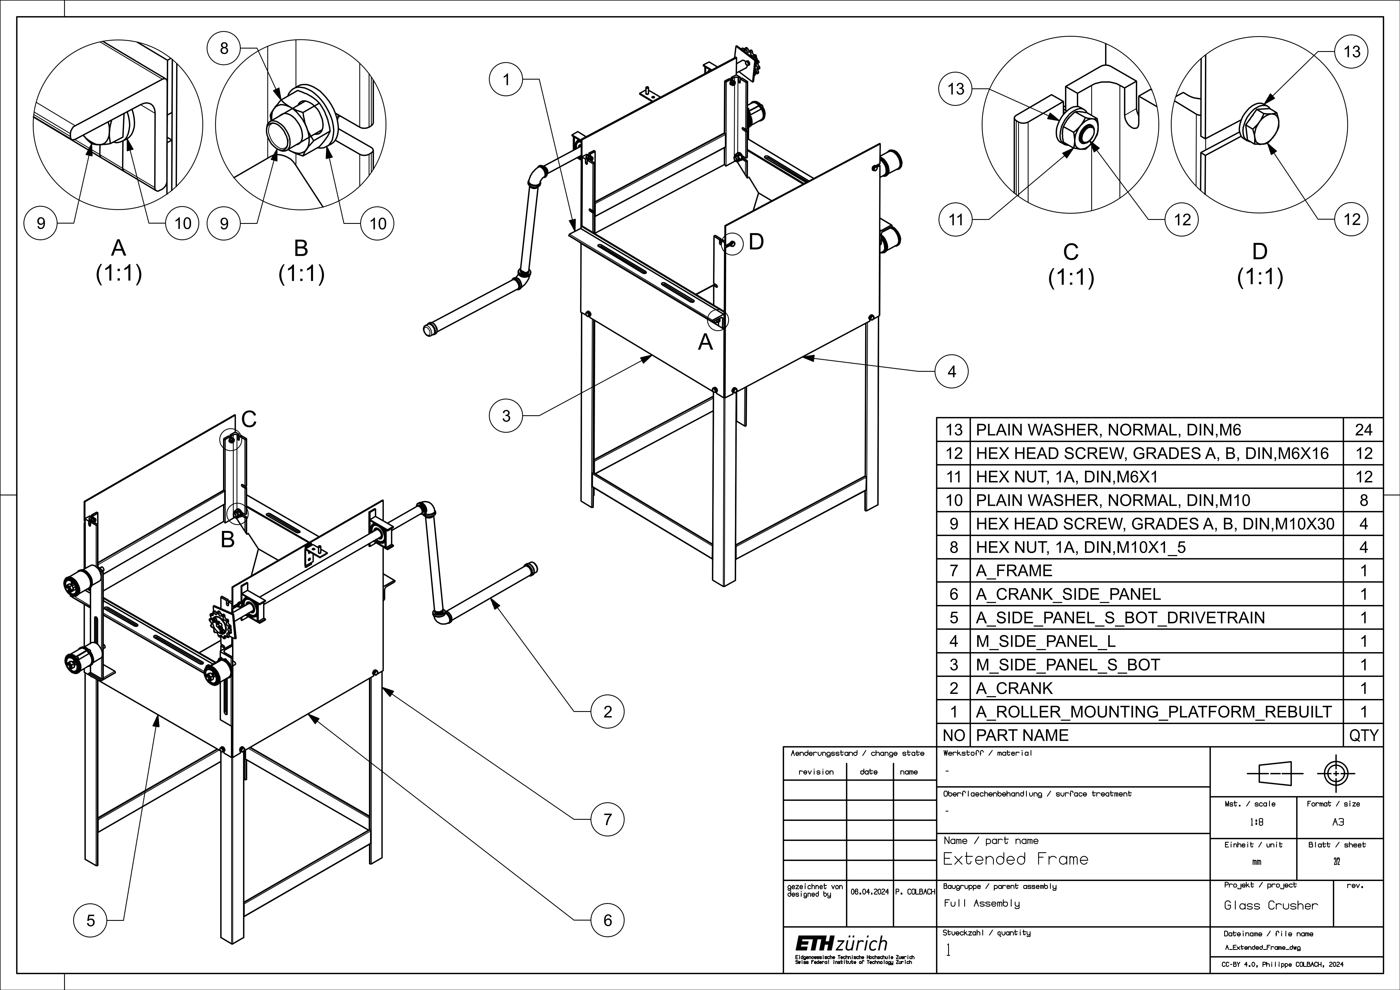
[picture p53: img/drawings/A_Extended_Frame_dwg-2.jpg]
Figure 36: Overview of the extended frame assembly.


Next, place the rollers (6) & (7) into the frame (10) and fasten them to the roller platforms - numbered part list shown in Figures 37 and 38. Add the upper side panels (4) & (5) and the cover structure (3). Attach the two sprocket modules (8) & (9) to the rollers, then add the chain connecting the crank to the first roller (2) and finally the chain connecting the two rollers to each other (1).

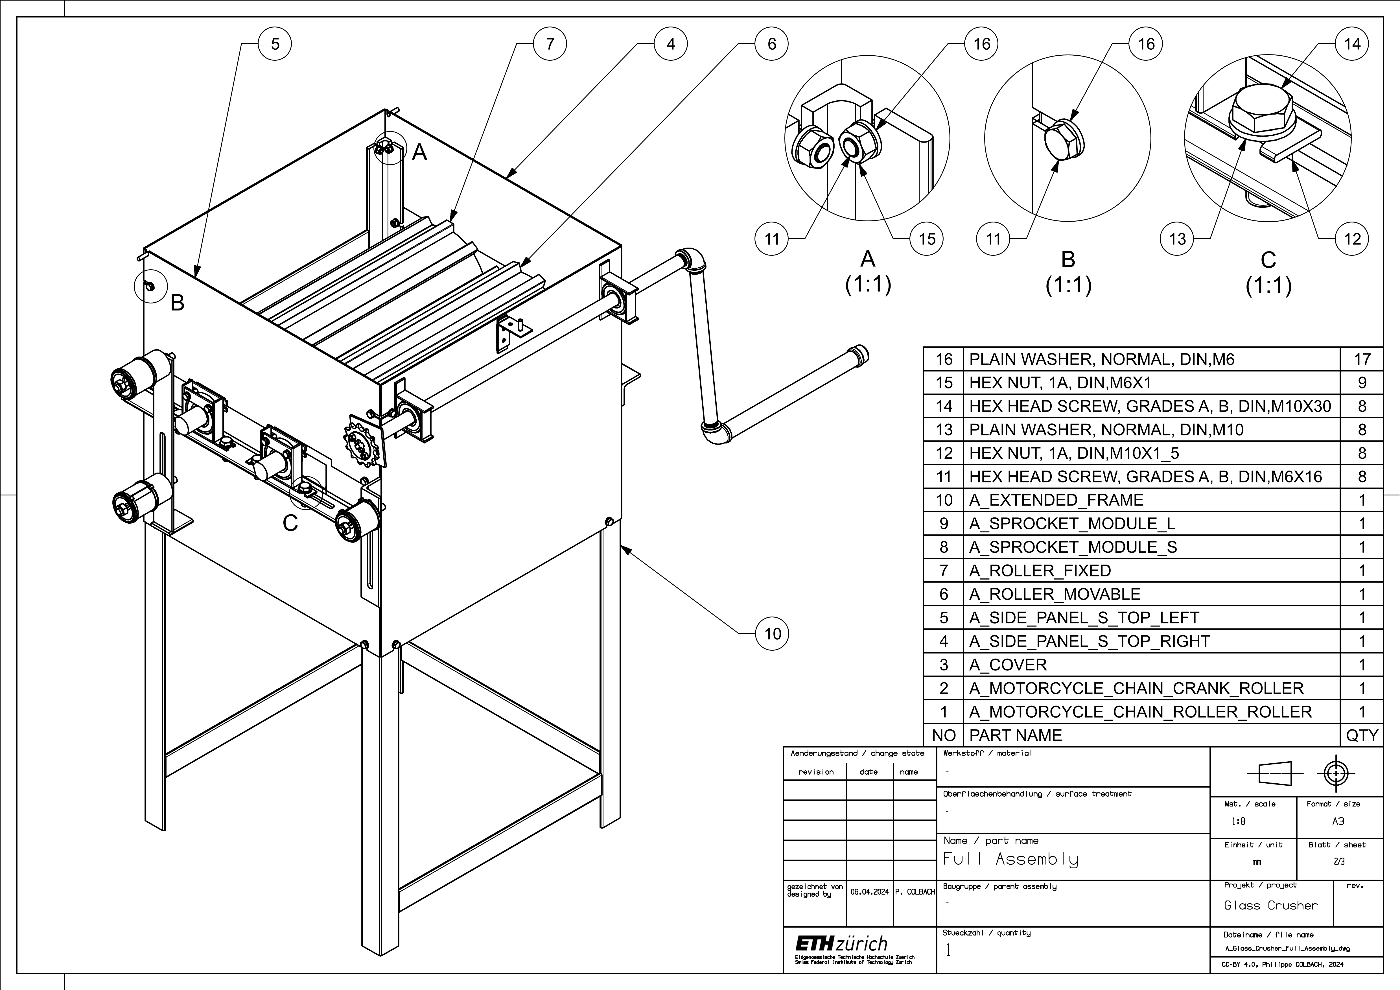
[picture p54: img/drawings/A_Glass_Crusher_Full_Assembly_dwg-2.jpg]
Figure 37: Top view of the full assembly - part list.


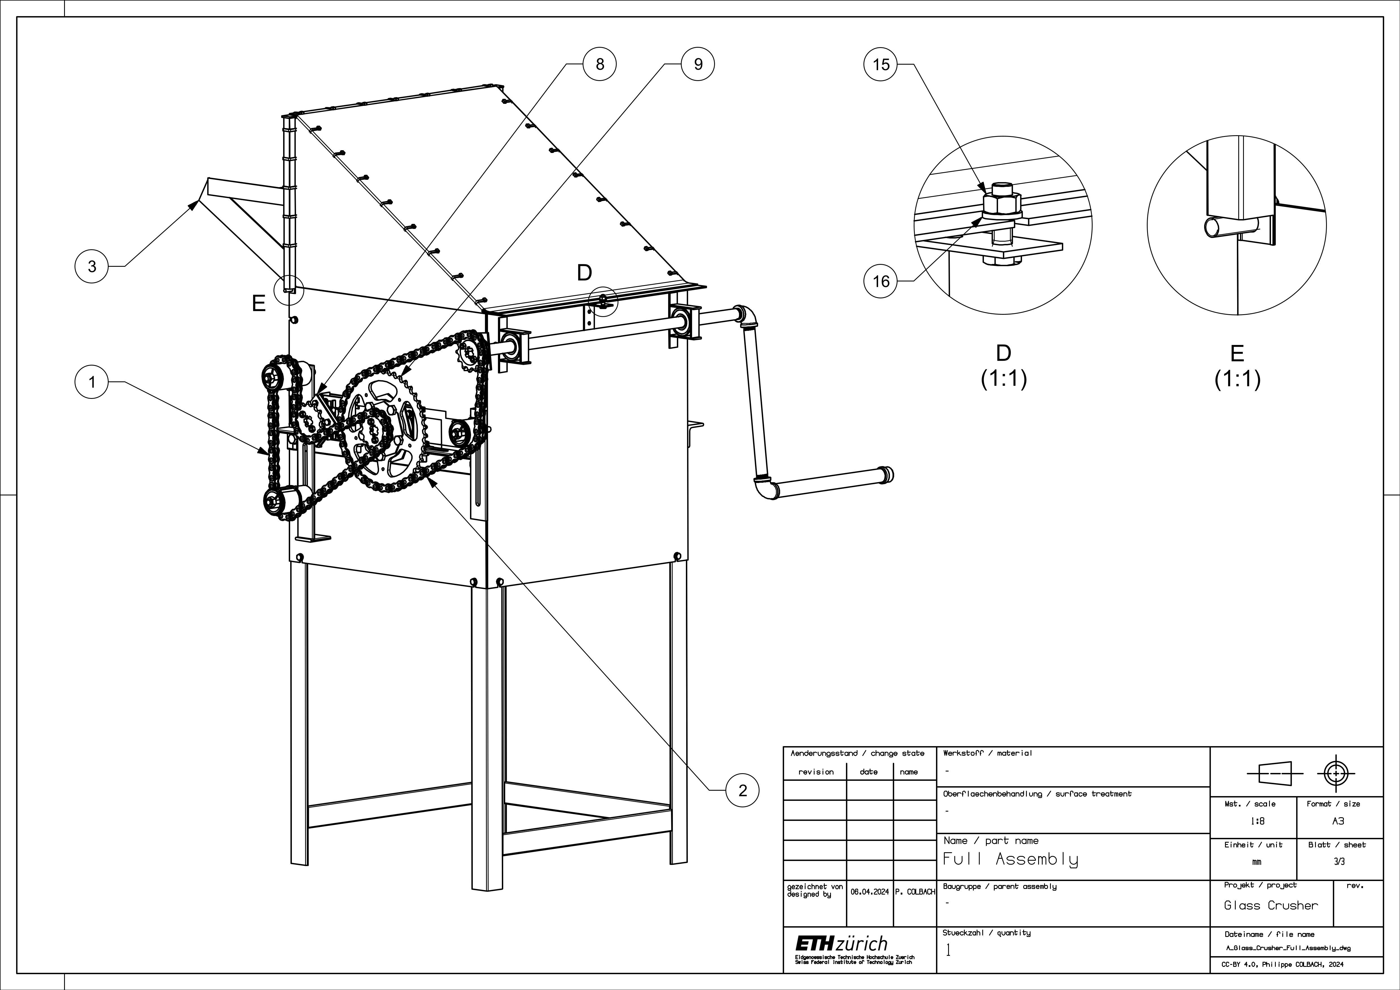
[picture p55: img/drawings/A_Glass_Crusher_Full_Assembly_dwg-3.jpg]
Figure 38: Side view of the full assembly - part list.


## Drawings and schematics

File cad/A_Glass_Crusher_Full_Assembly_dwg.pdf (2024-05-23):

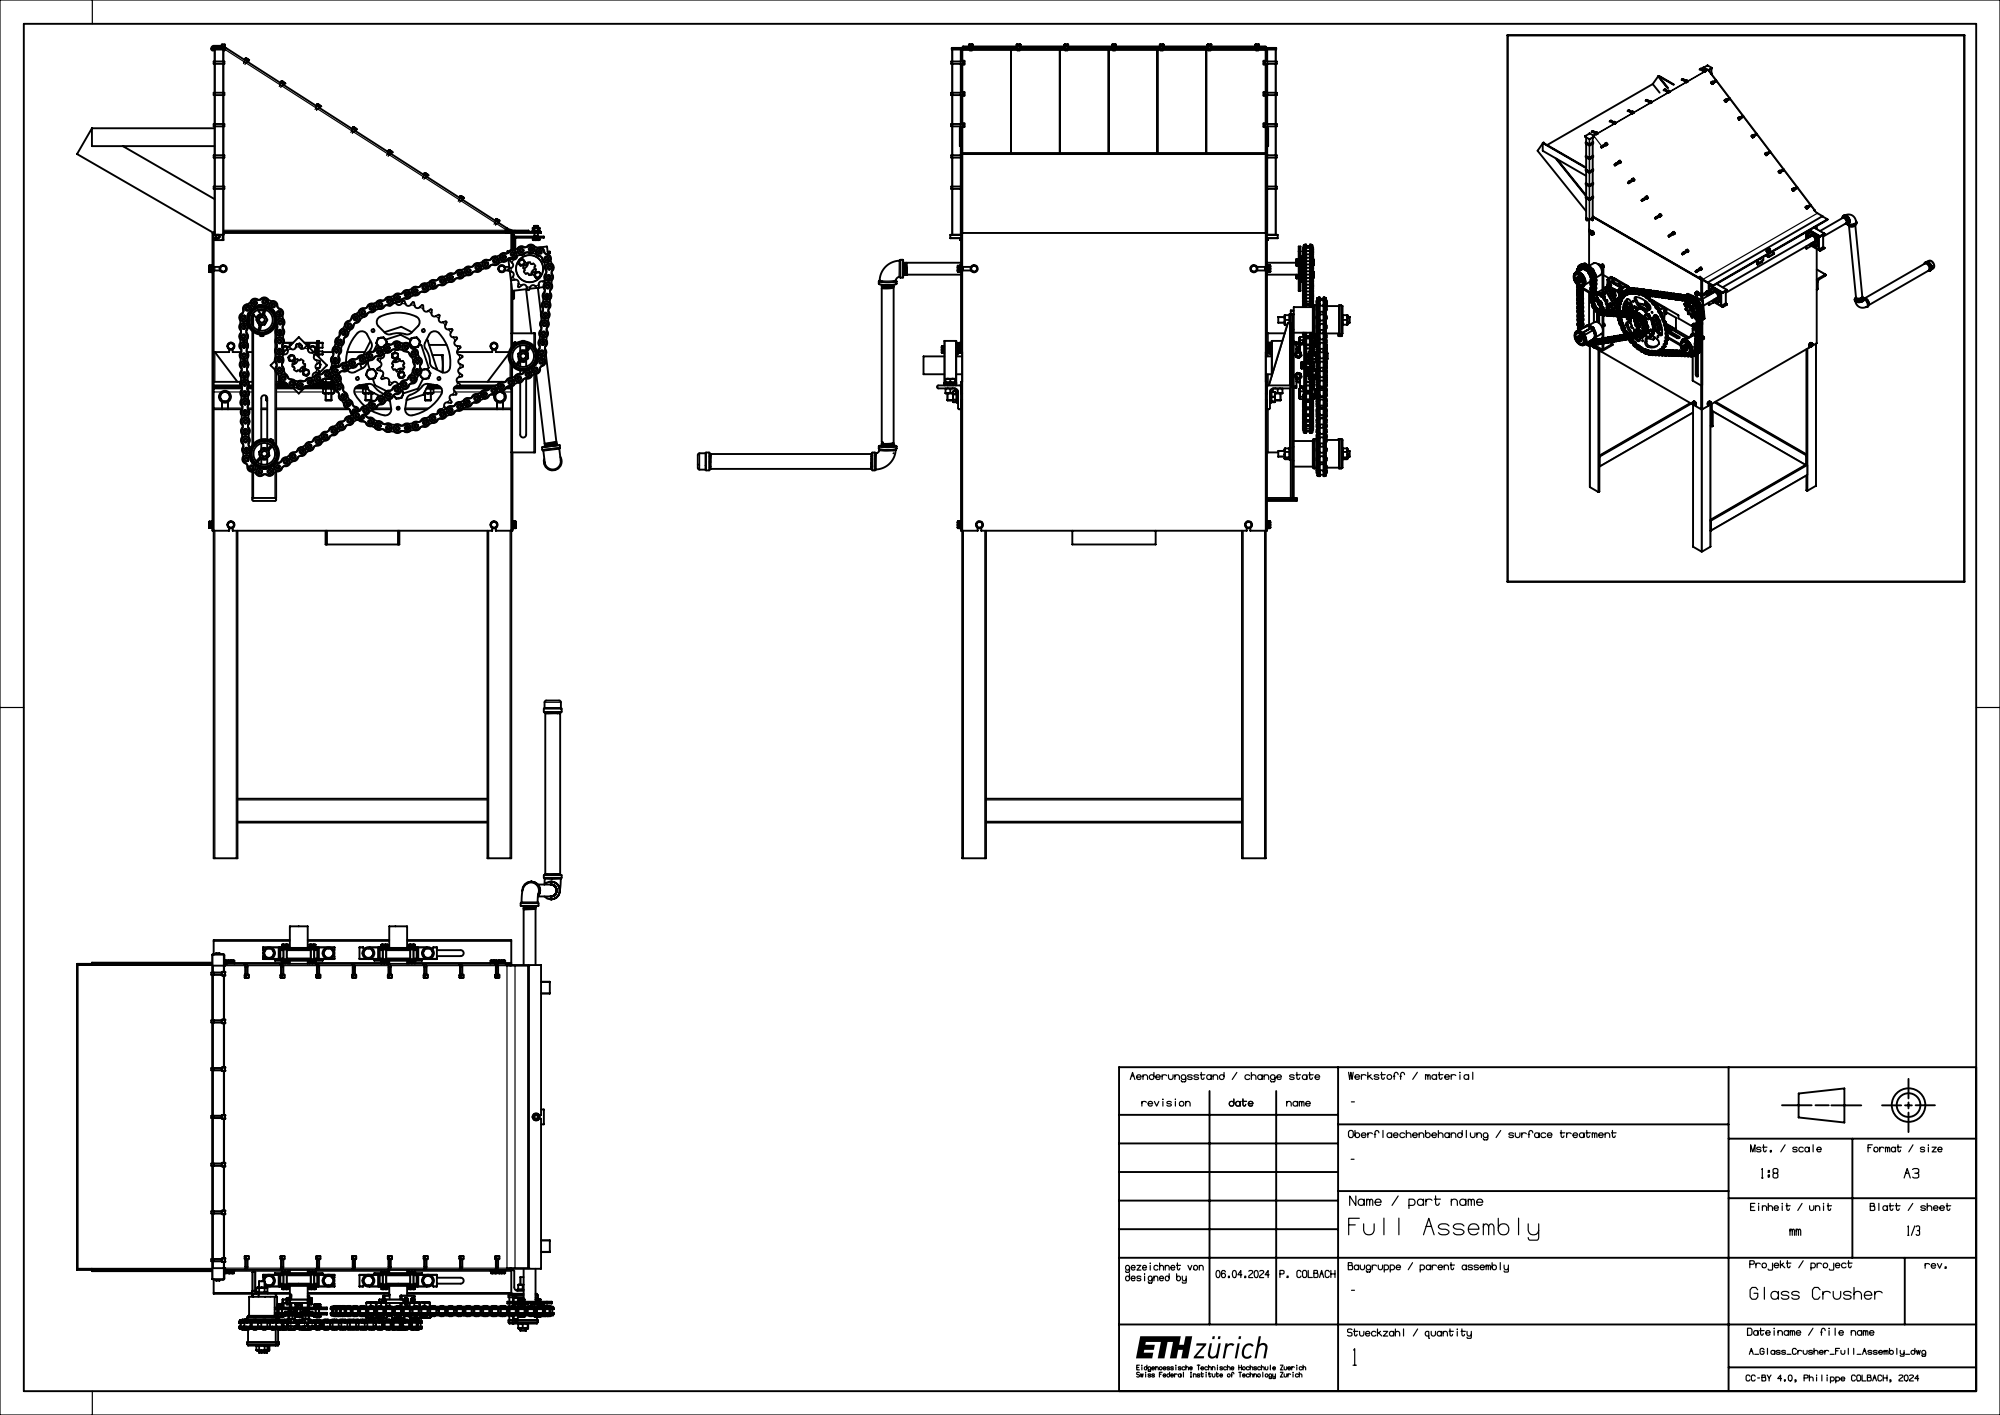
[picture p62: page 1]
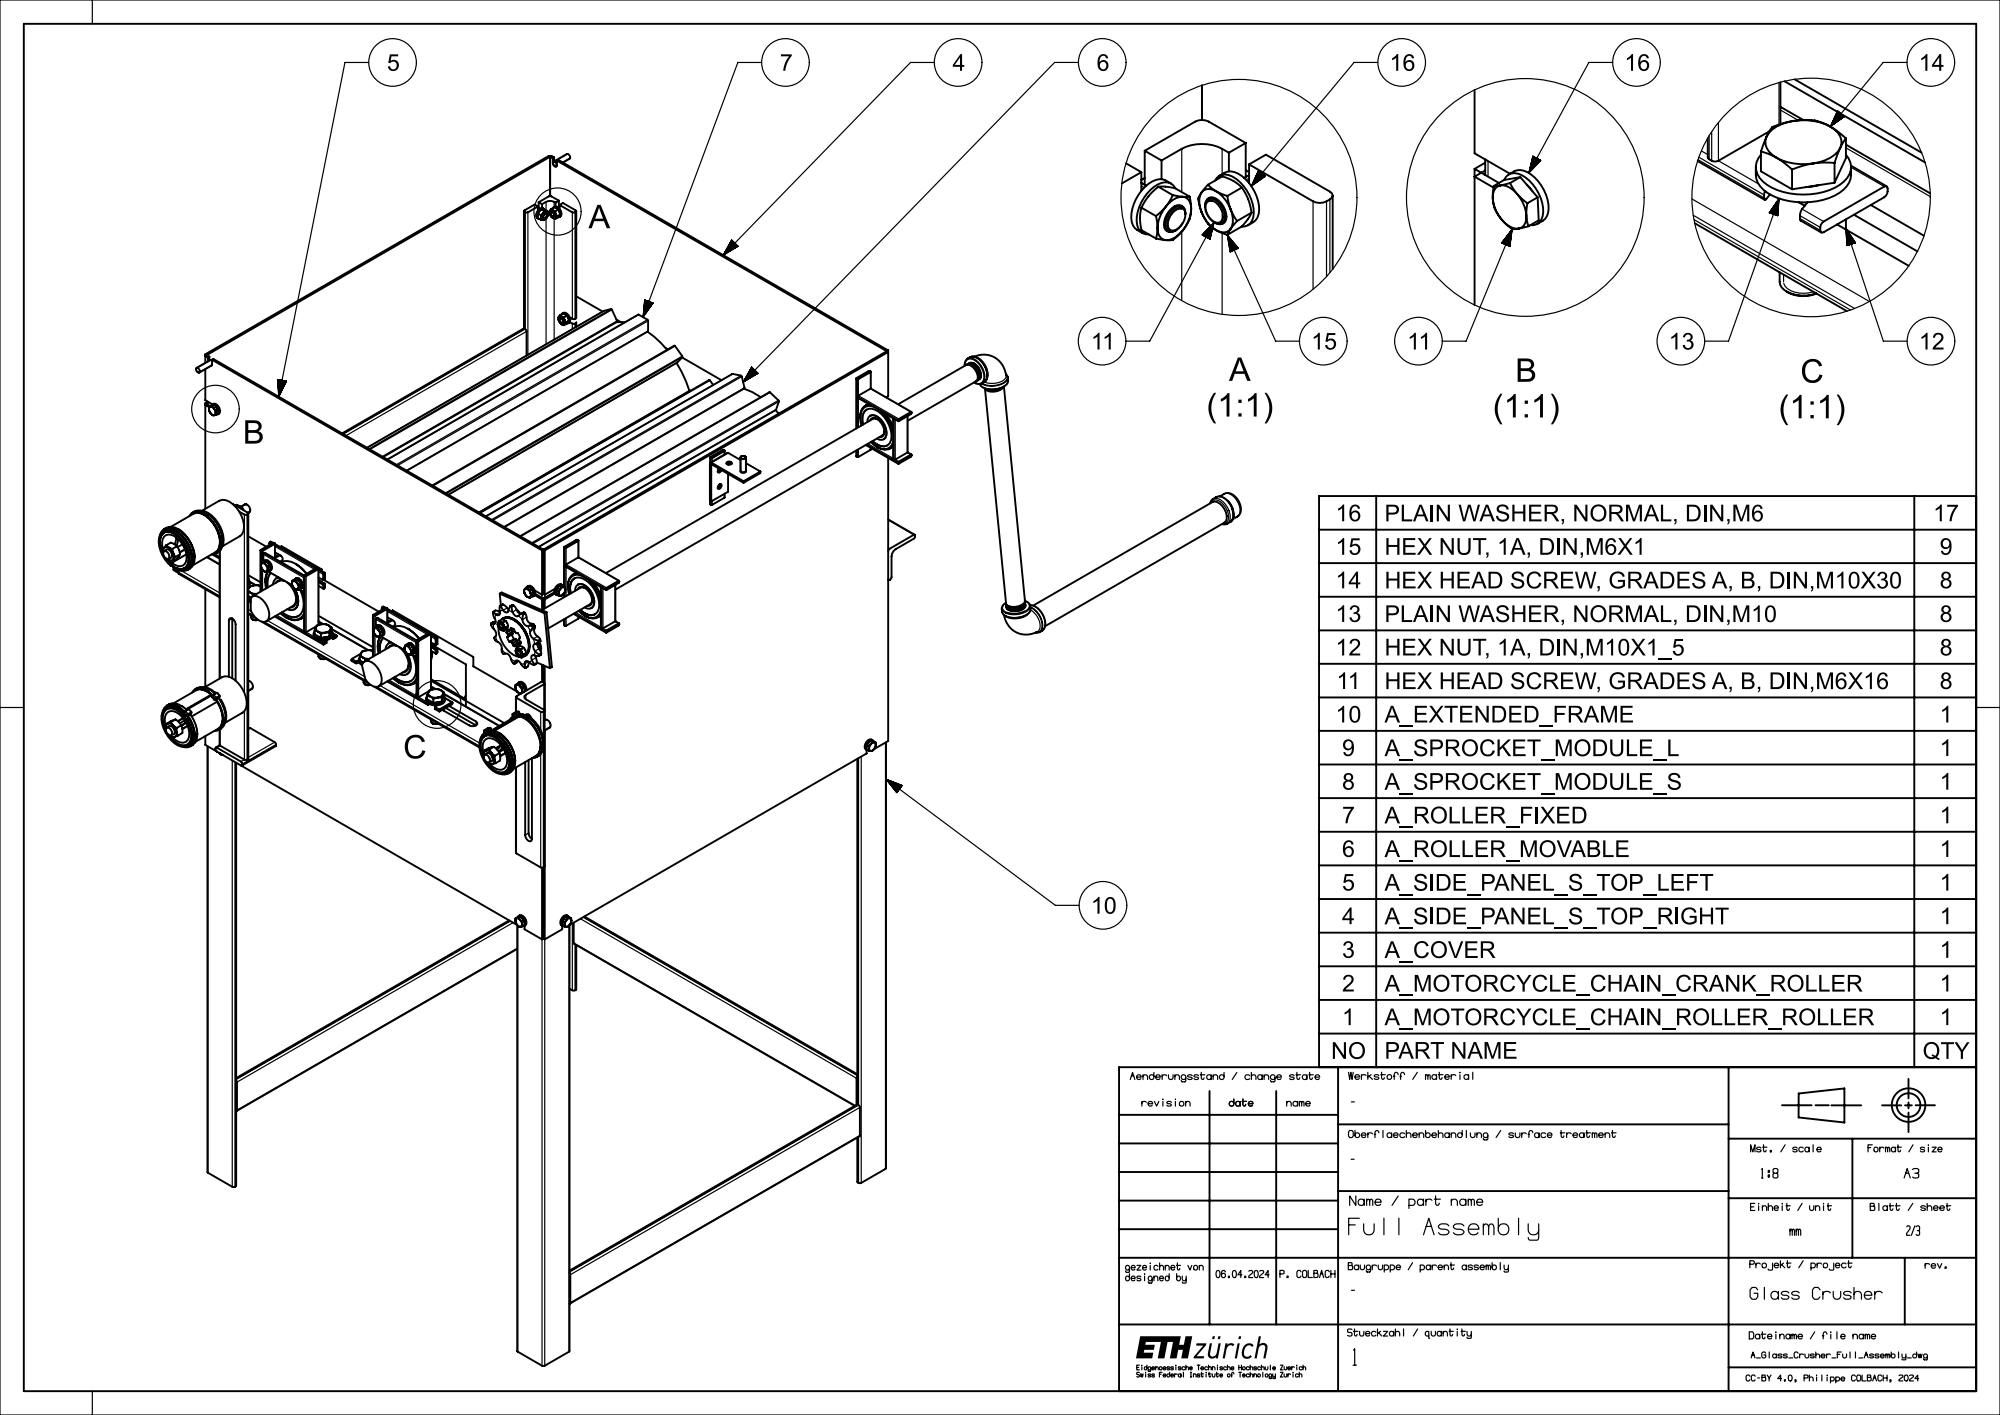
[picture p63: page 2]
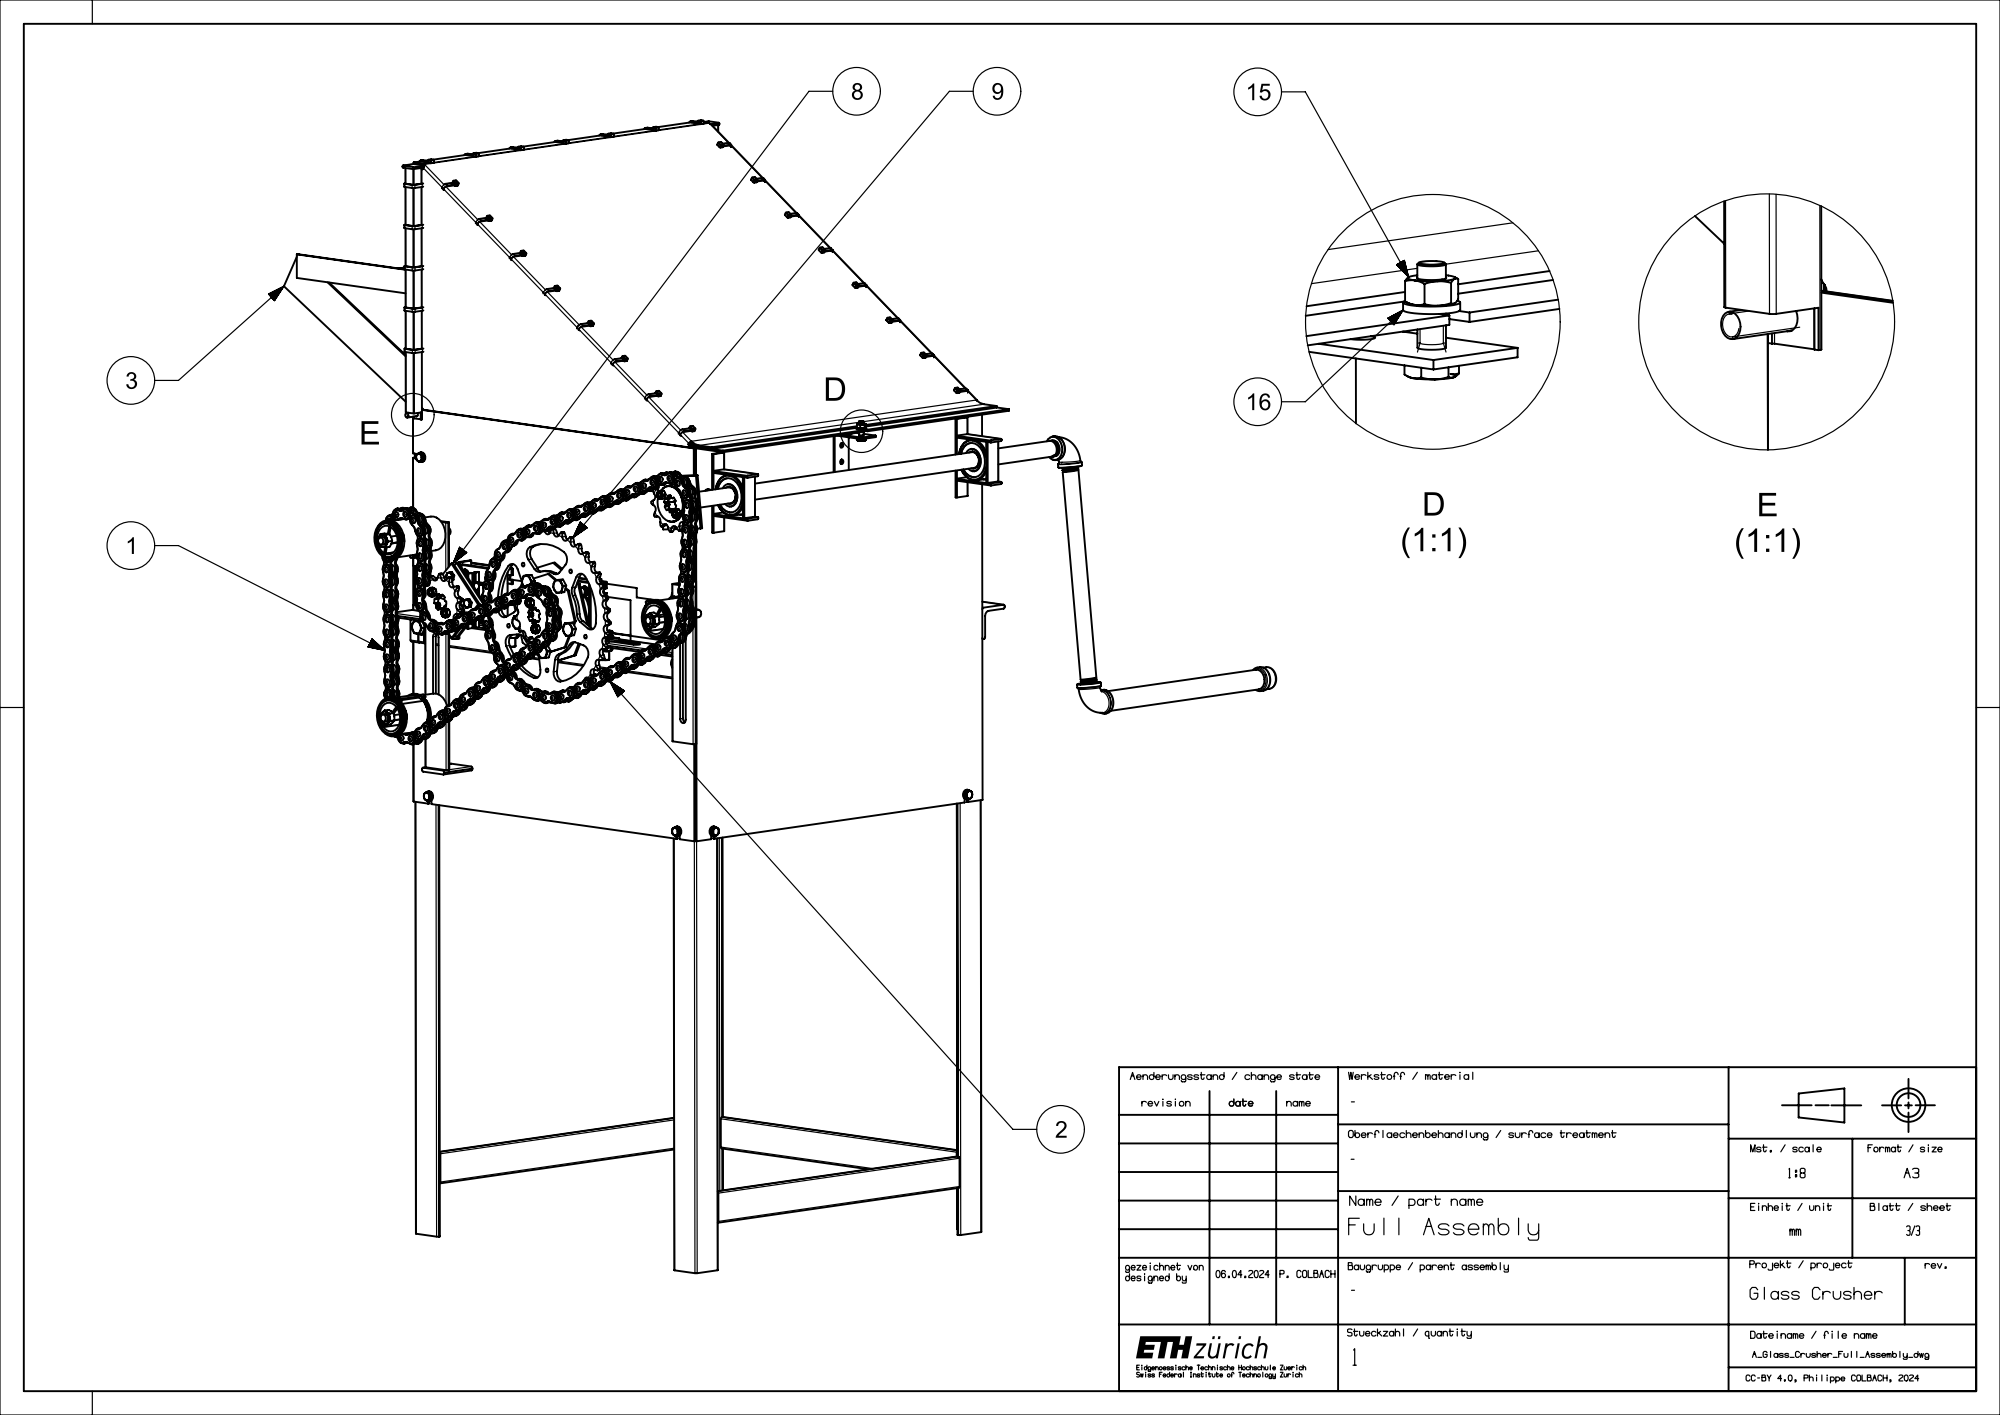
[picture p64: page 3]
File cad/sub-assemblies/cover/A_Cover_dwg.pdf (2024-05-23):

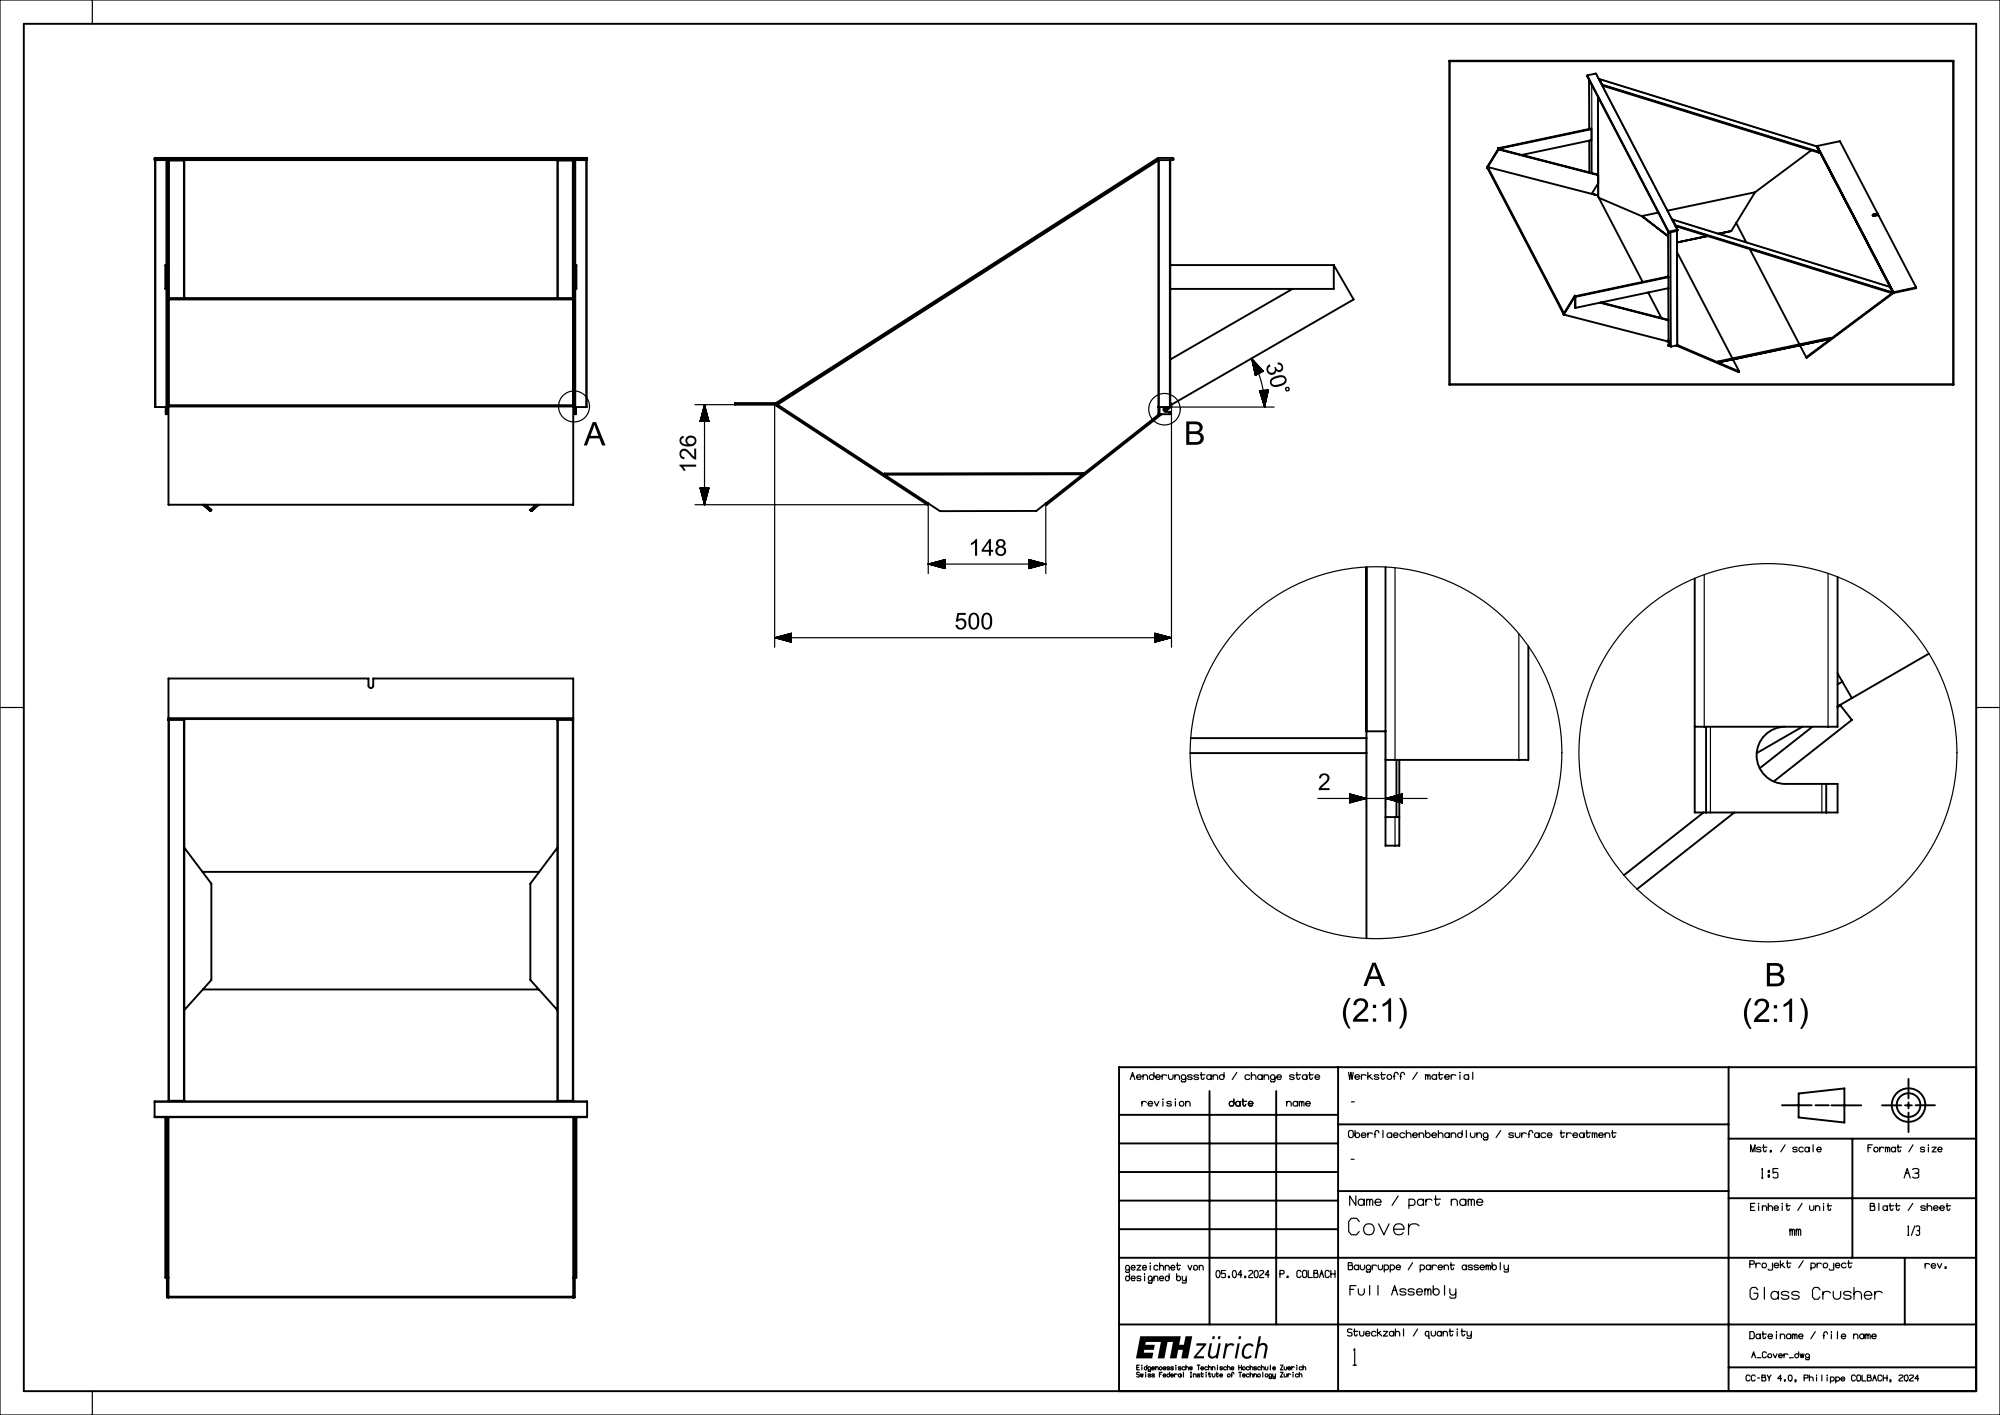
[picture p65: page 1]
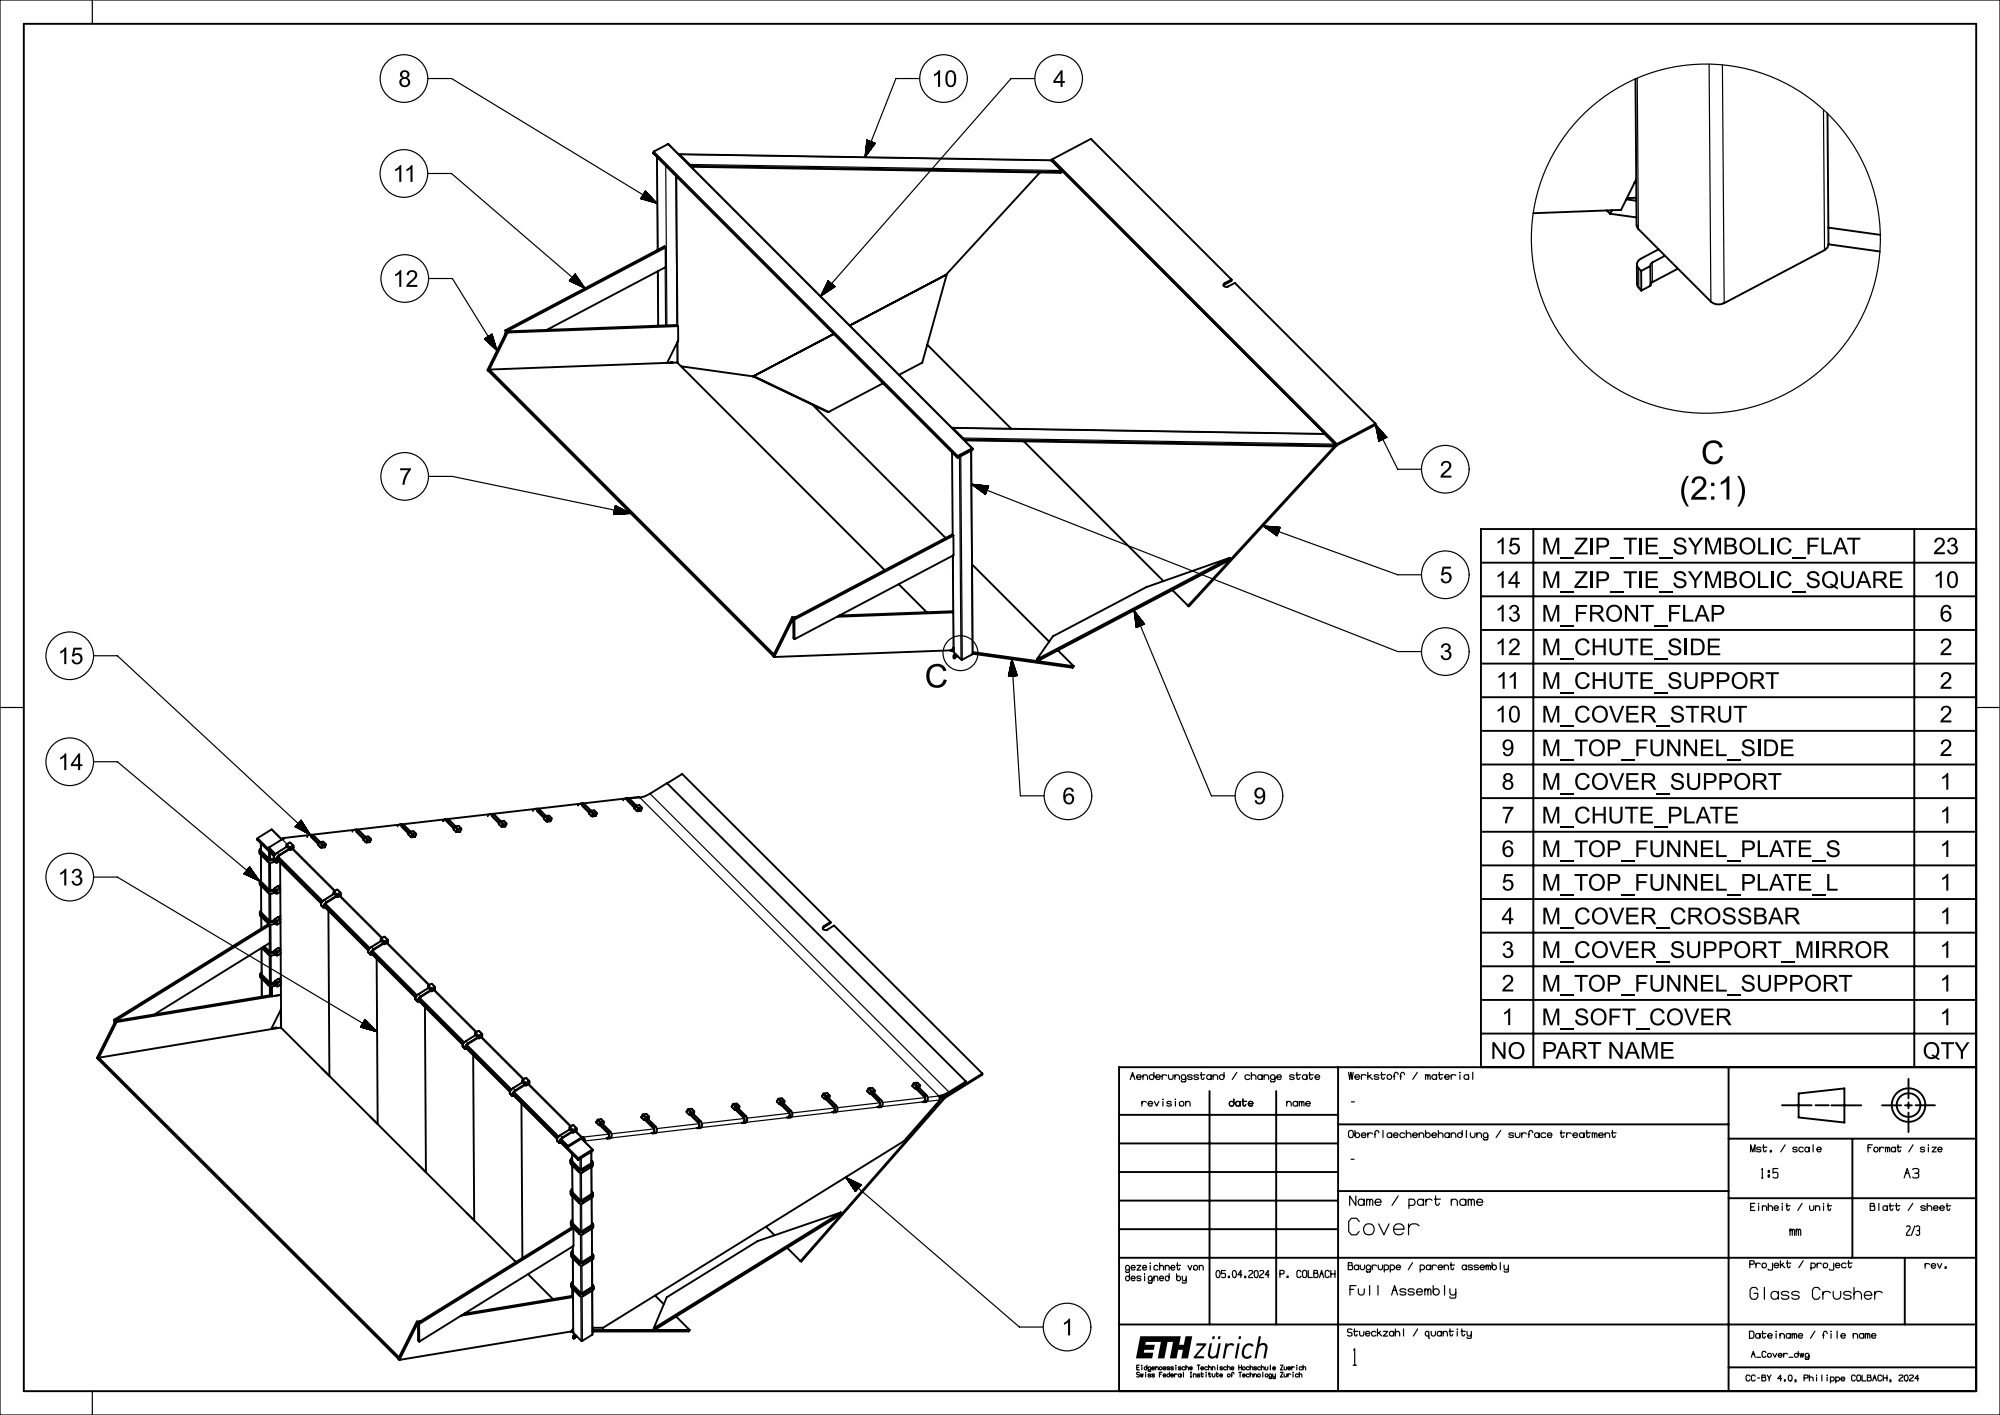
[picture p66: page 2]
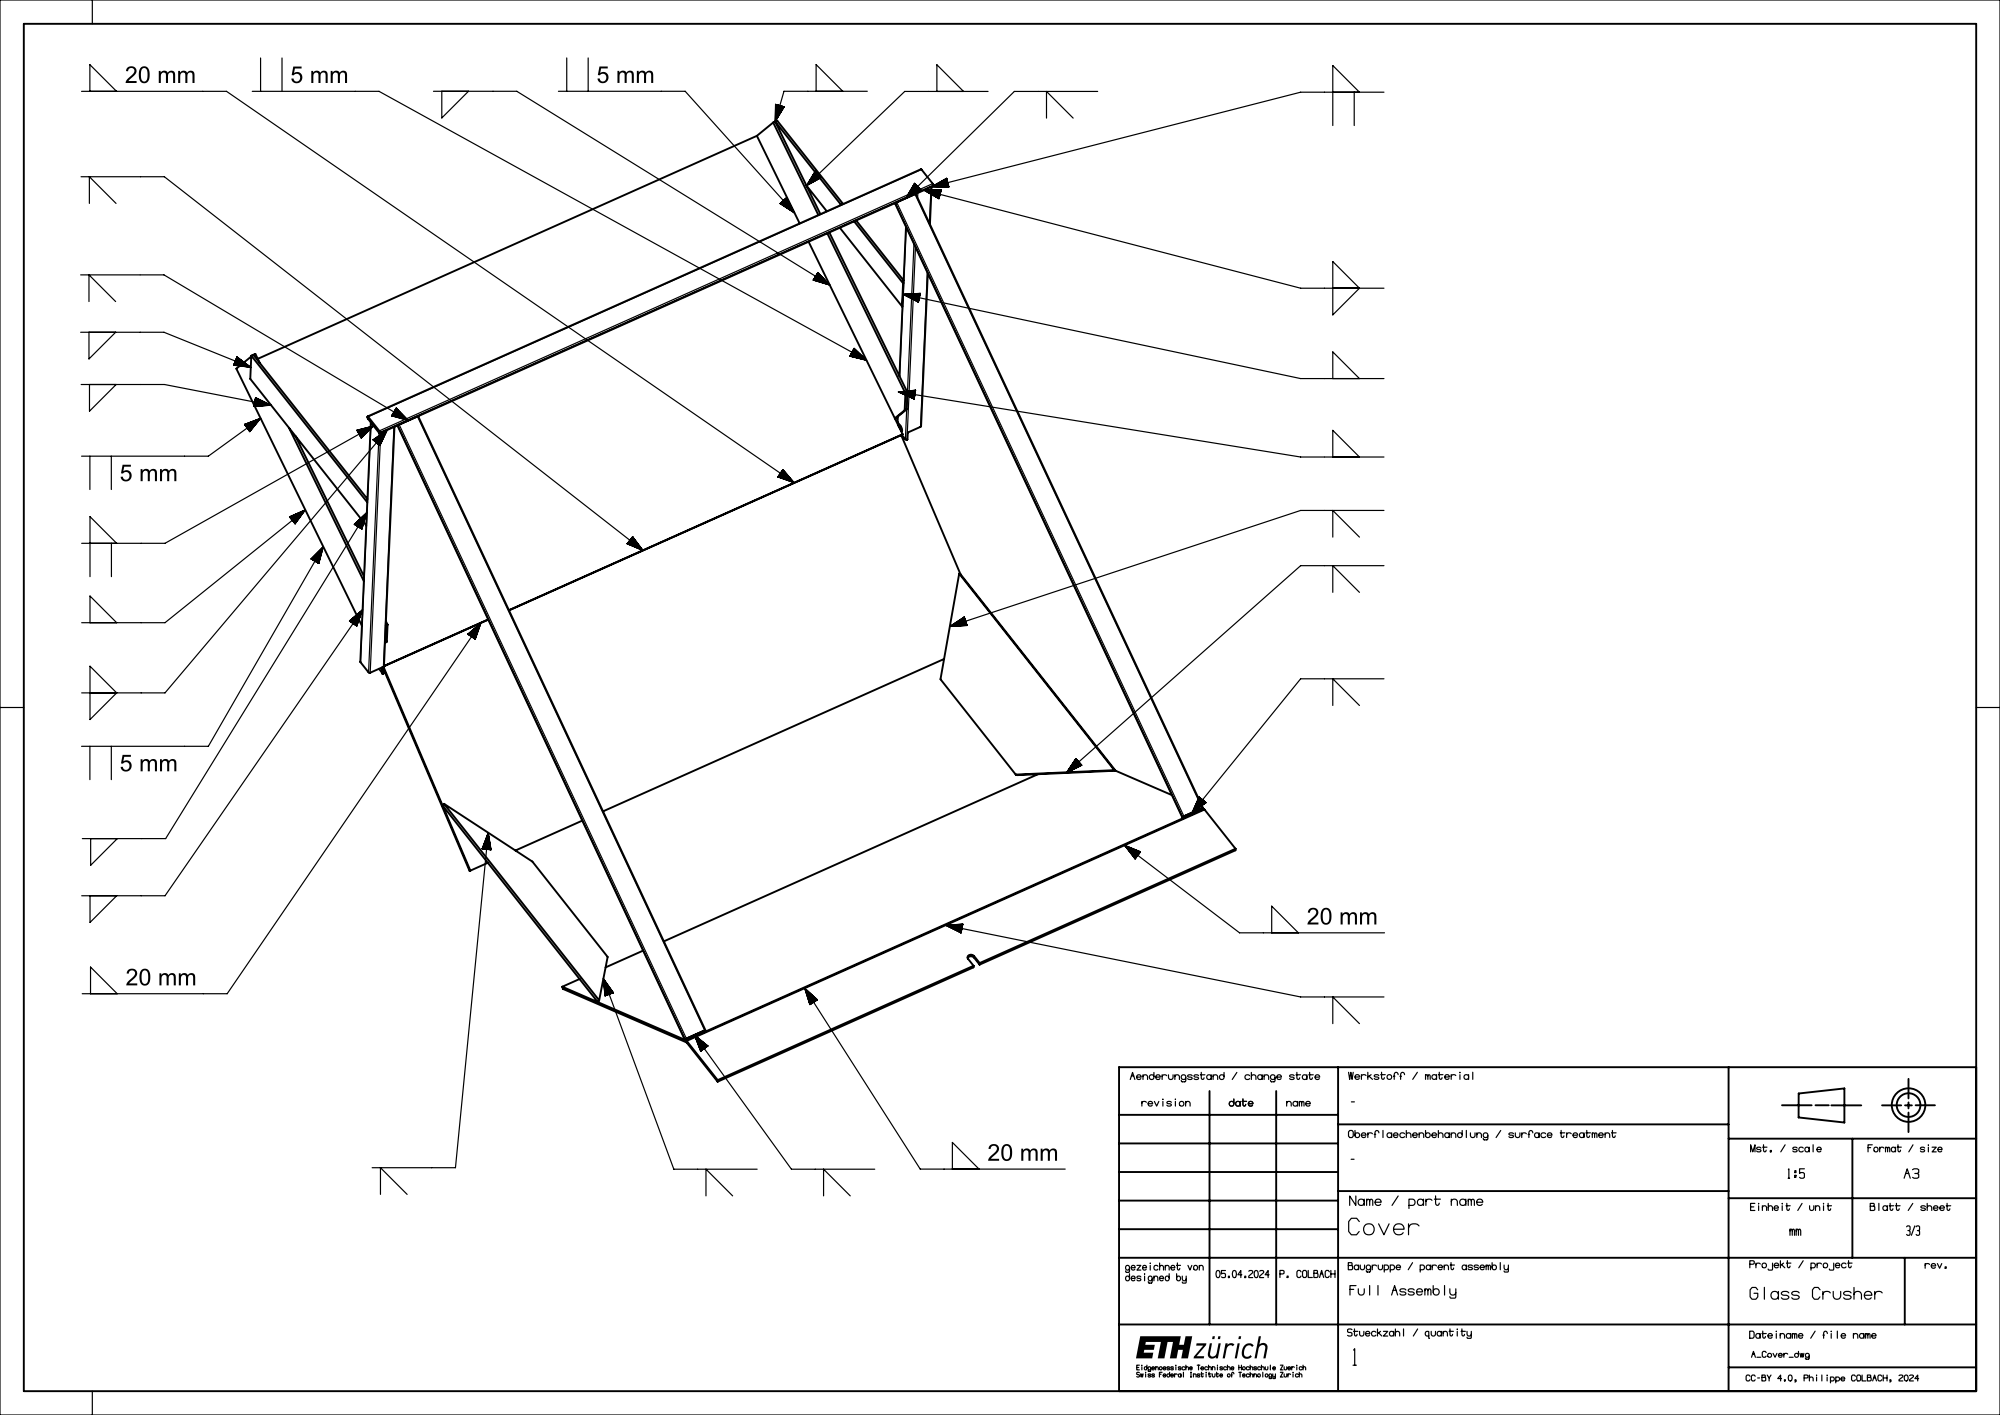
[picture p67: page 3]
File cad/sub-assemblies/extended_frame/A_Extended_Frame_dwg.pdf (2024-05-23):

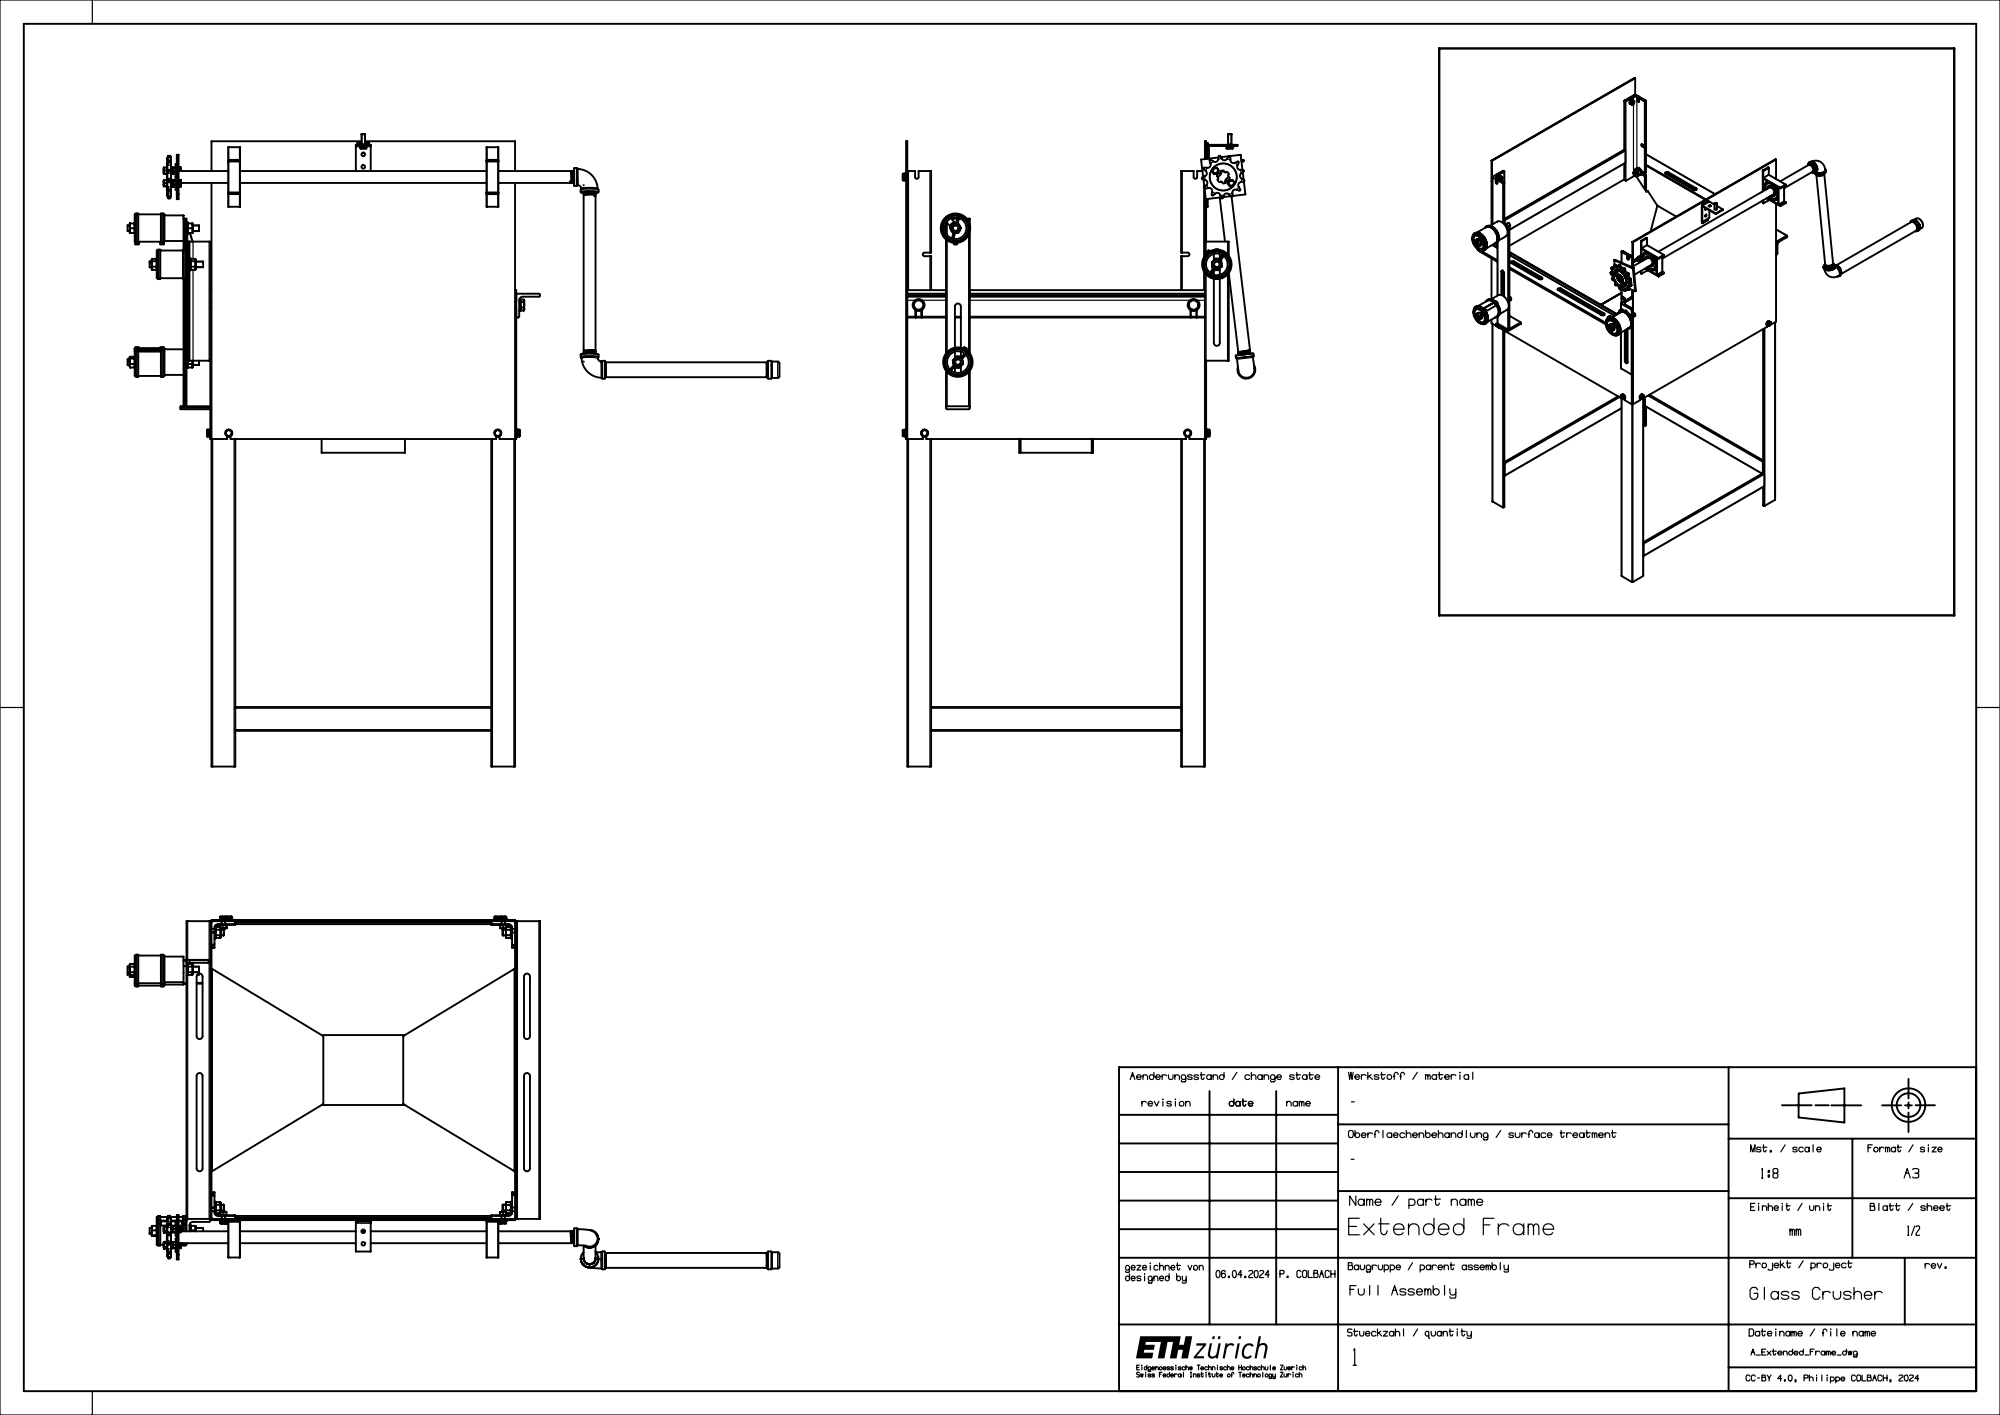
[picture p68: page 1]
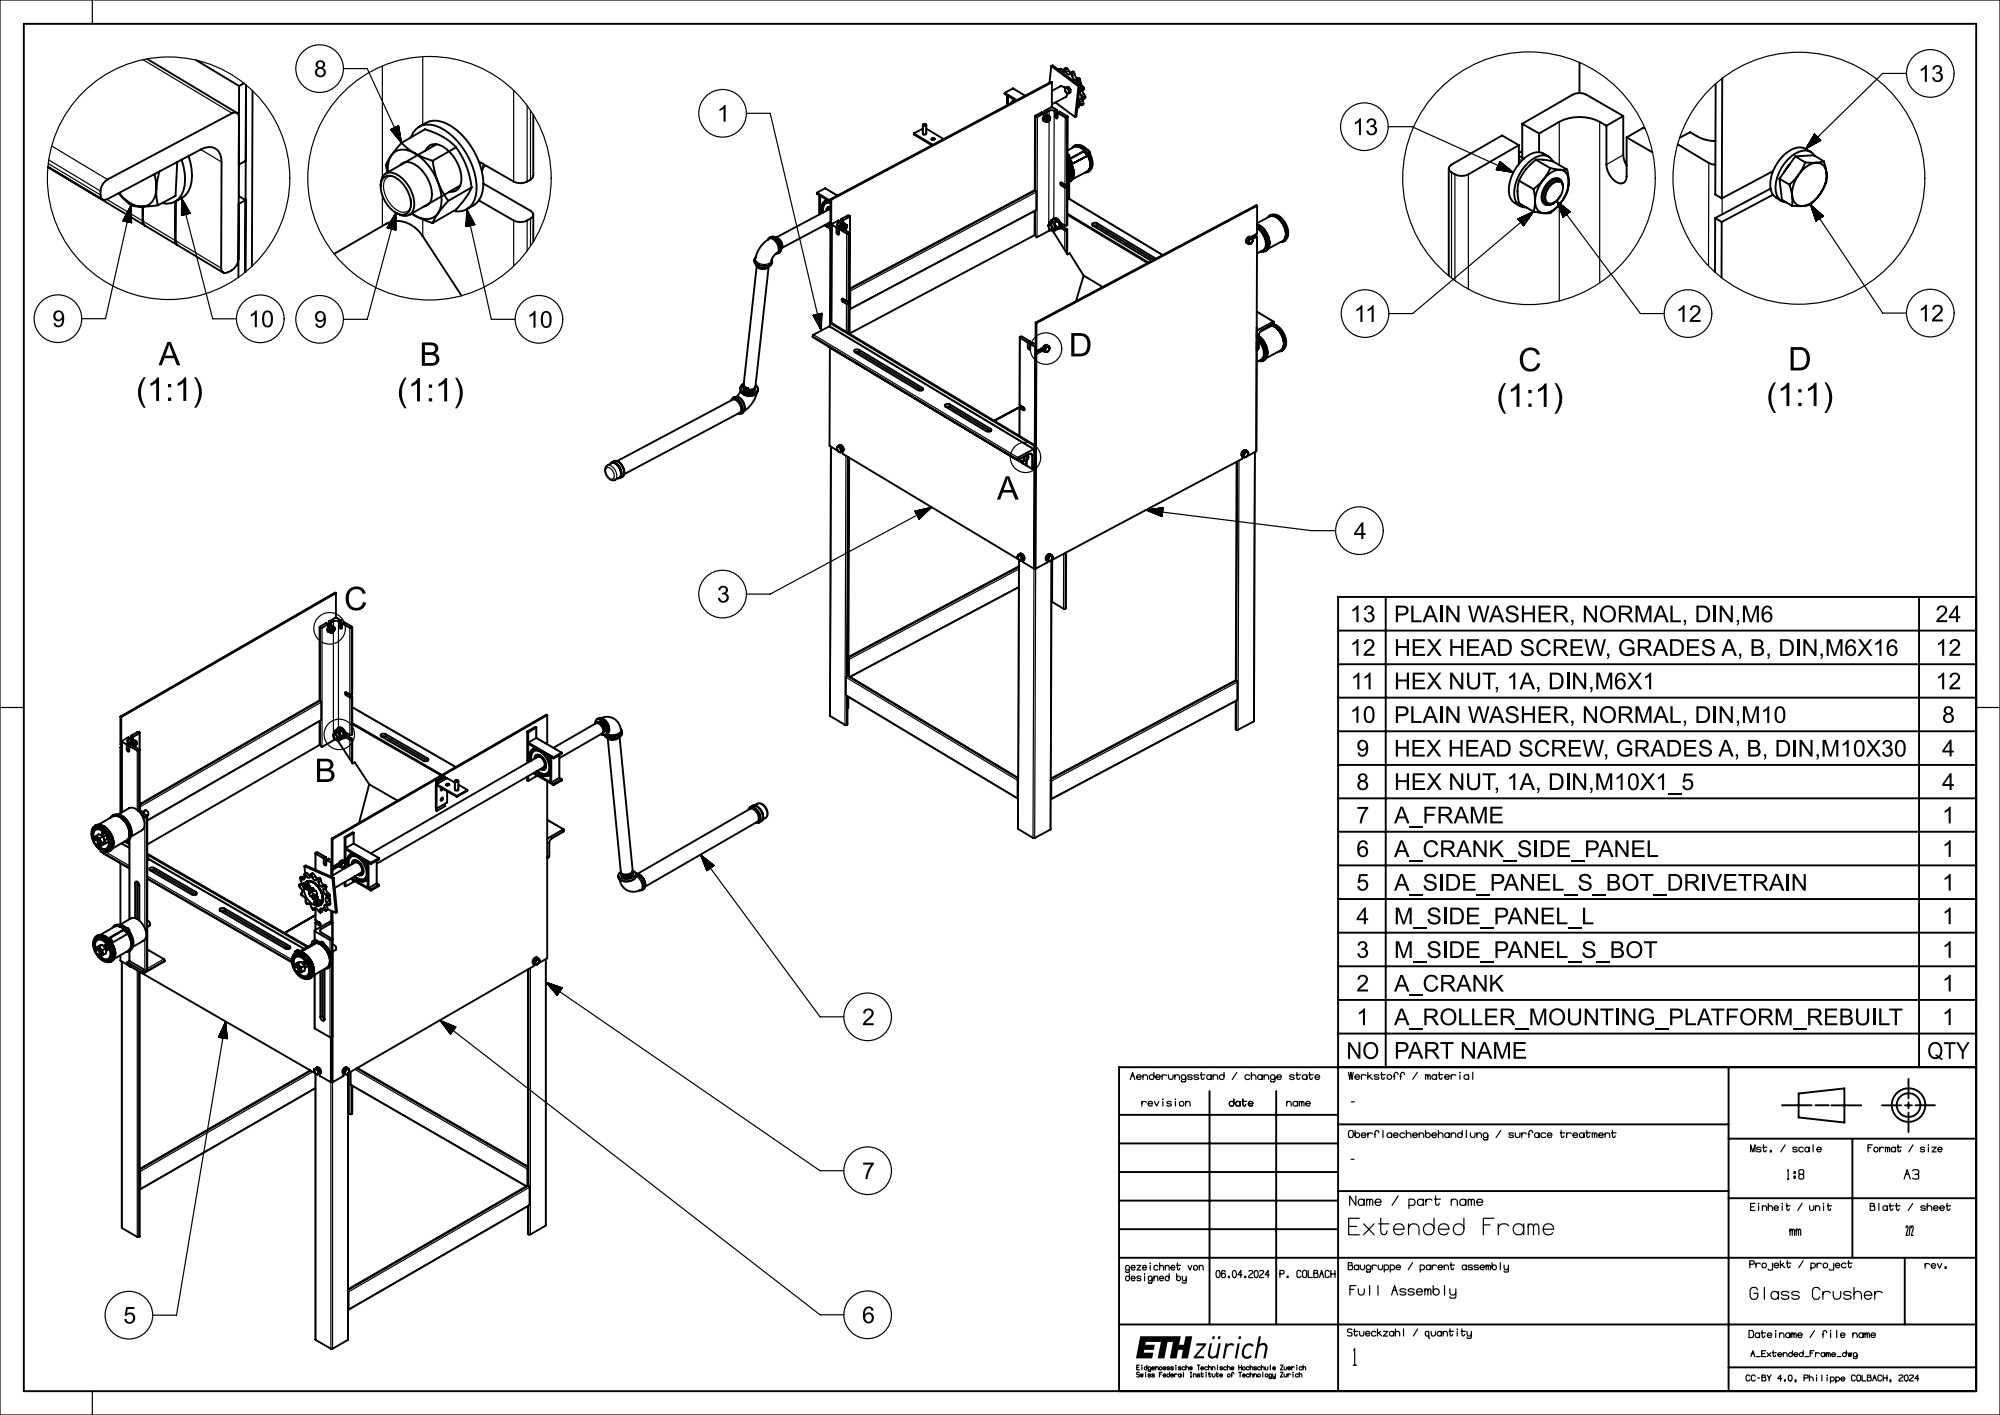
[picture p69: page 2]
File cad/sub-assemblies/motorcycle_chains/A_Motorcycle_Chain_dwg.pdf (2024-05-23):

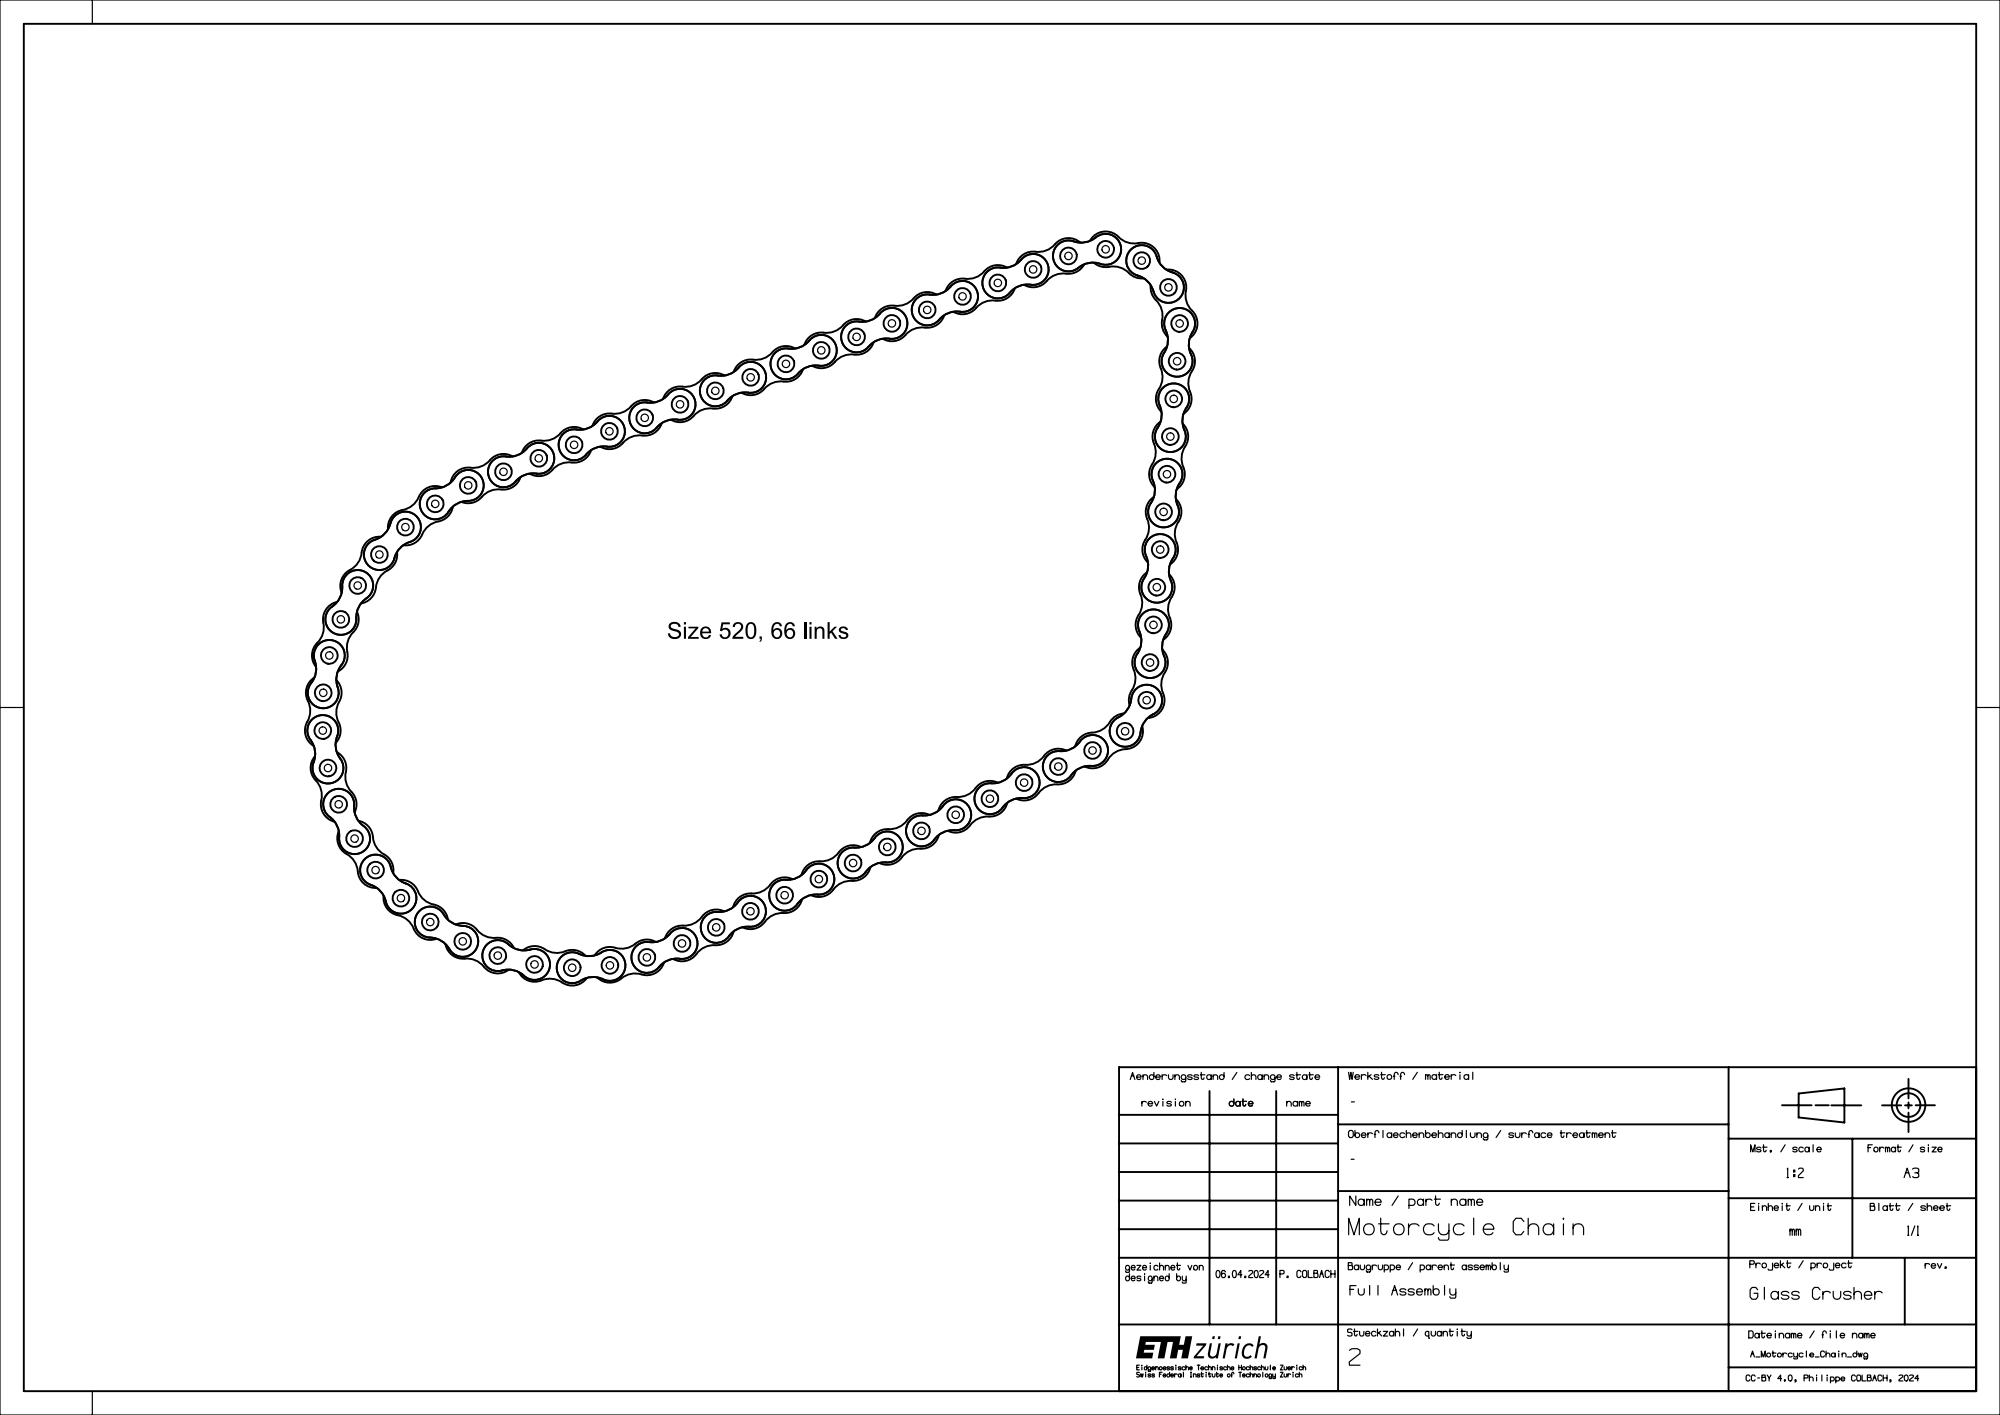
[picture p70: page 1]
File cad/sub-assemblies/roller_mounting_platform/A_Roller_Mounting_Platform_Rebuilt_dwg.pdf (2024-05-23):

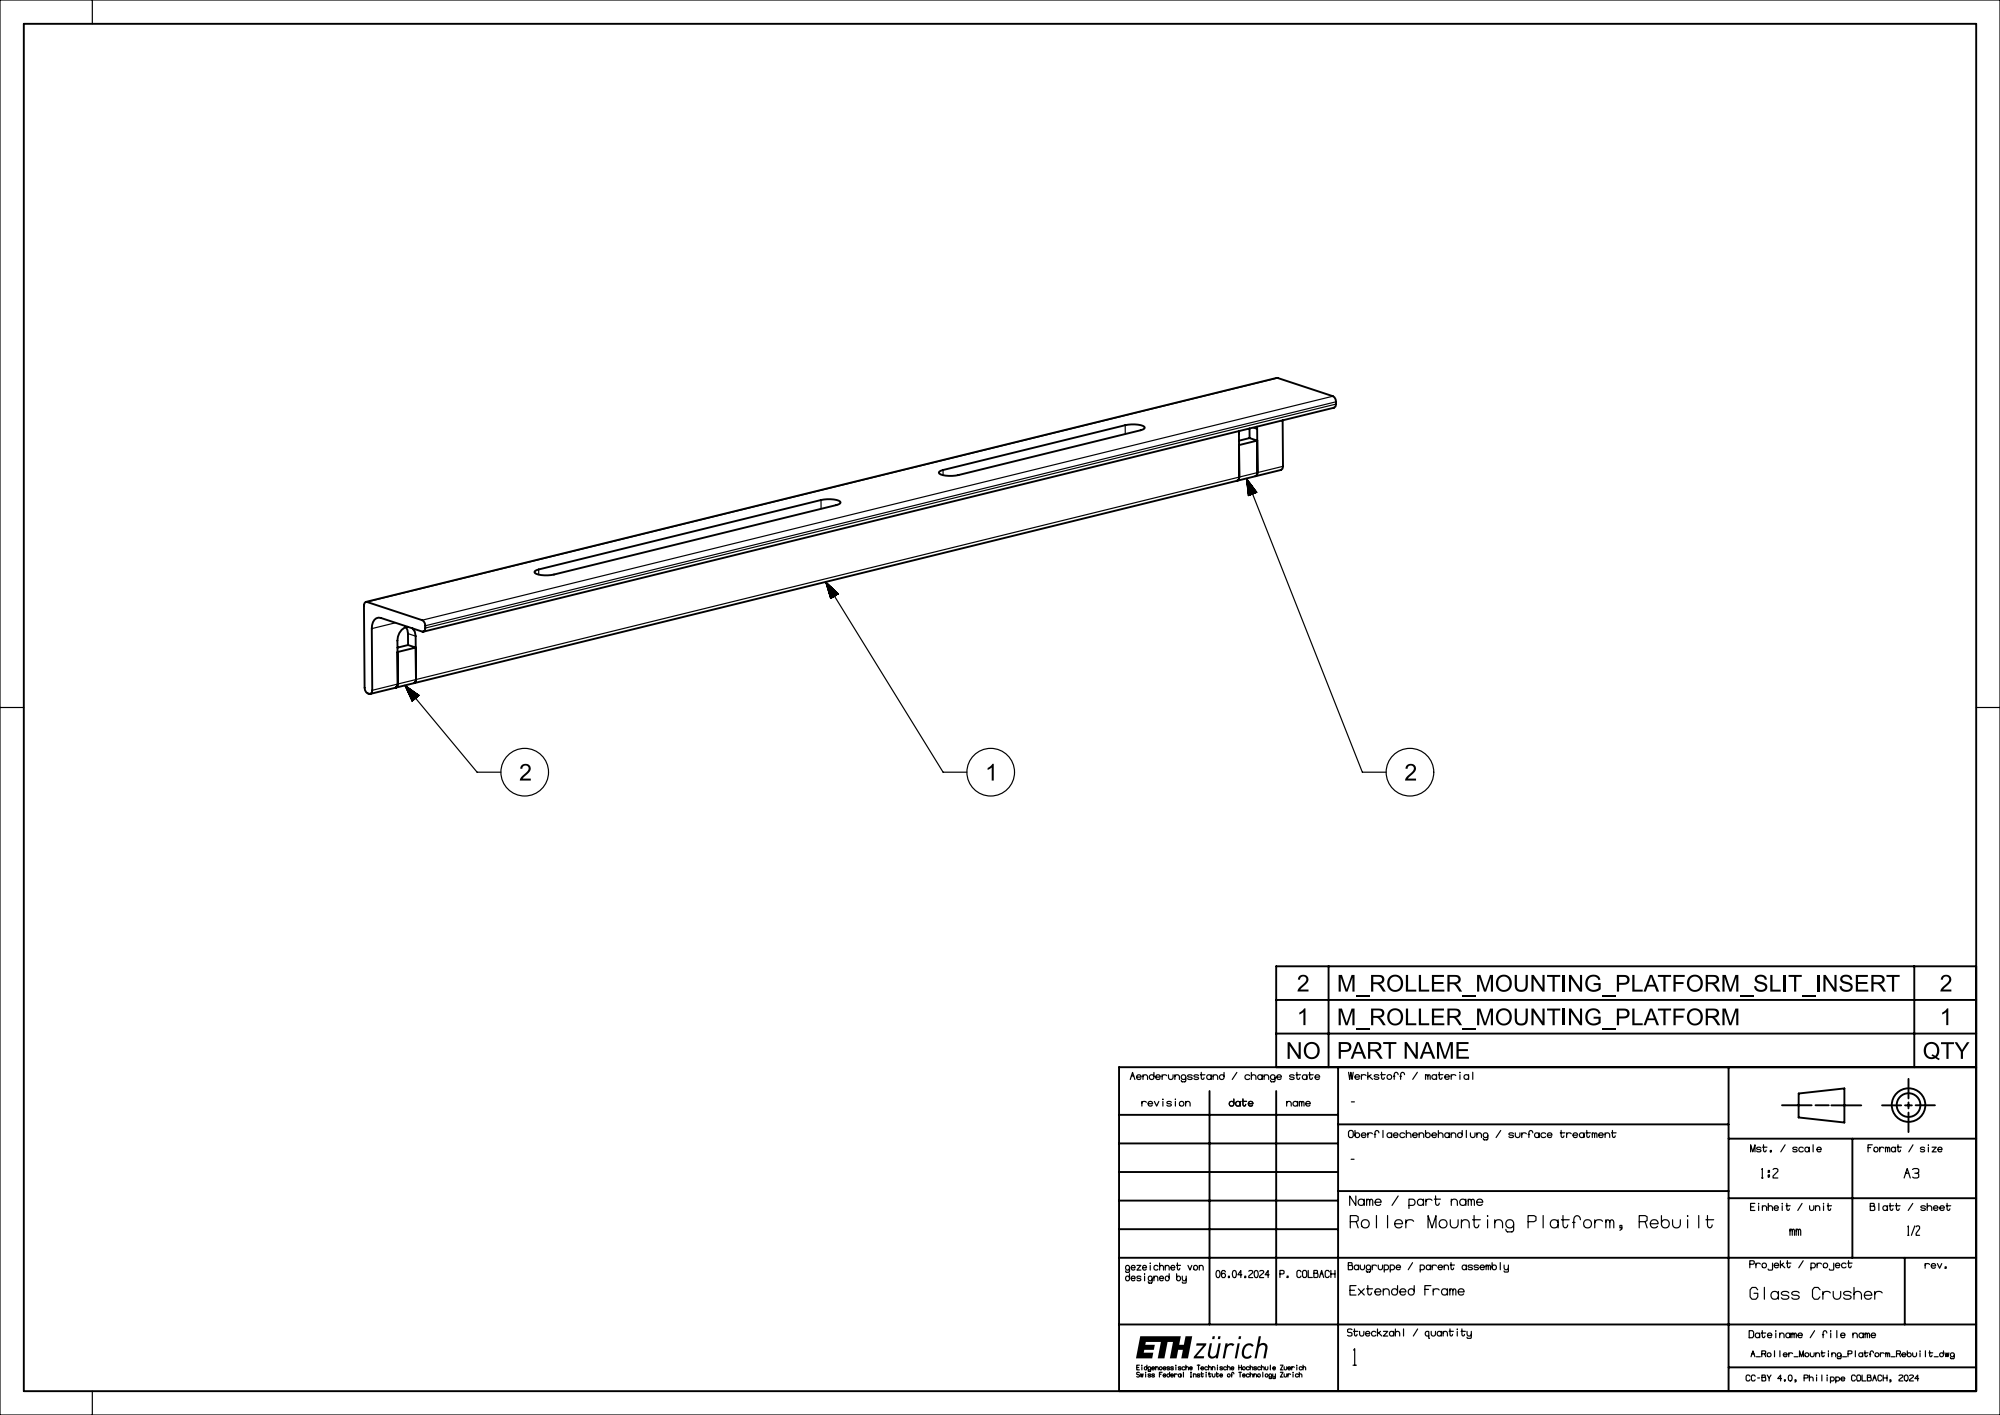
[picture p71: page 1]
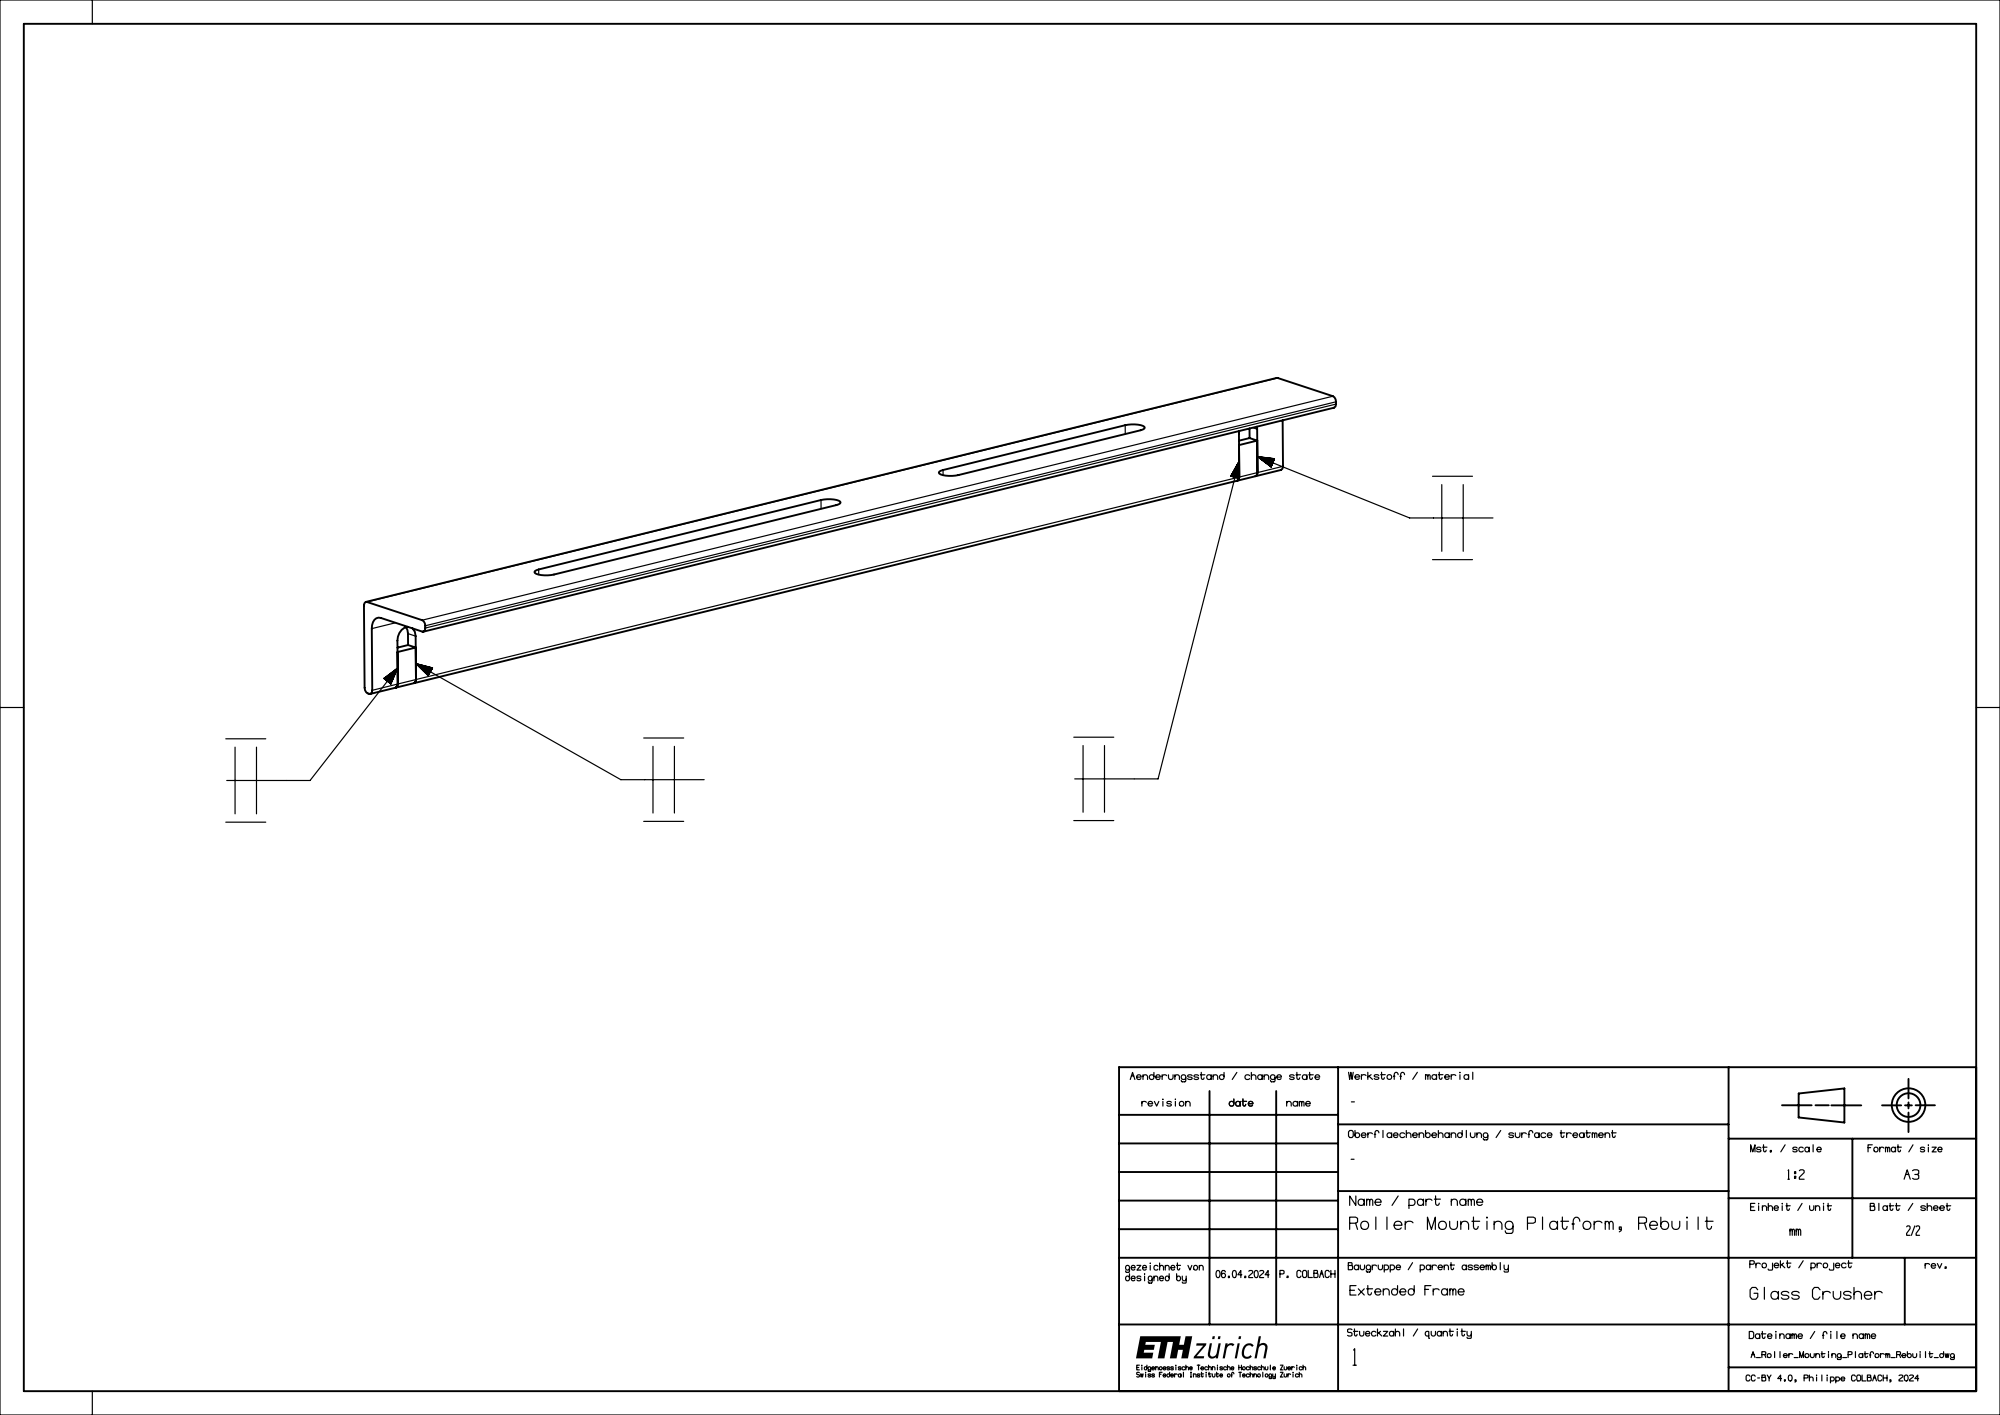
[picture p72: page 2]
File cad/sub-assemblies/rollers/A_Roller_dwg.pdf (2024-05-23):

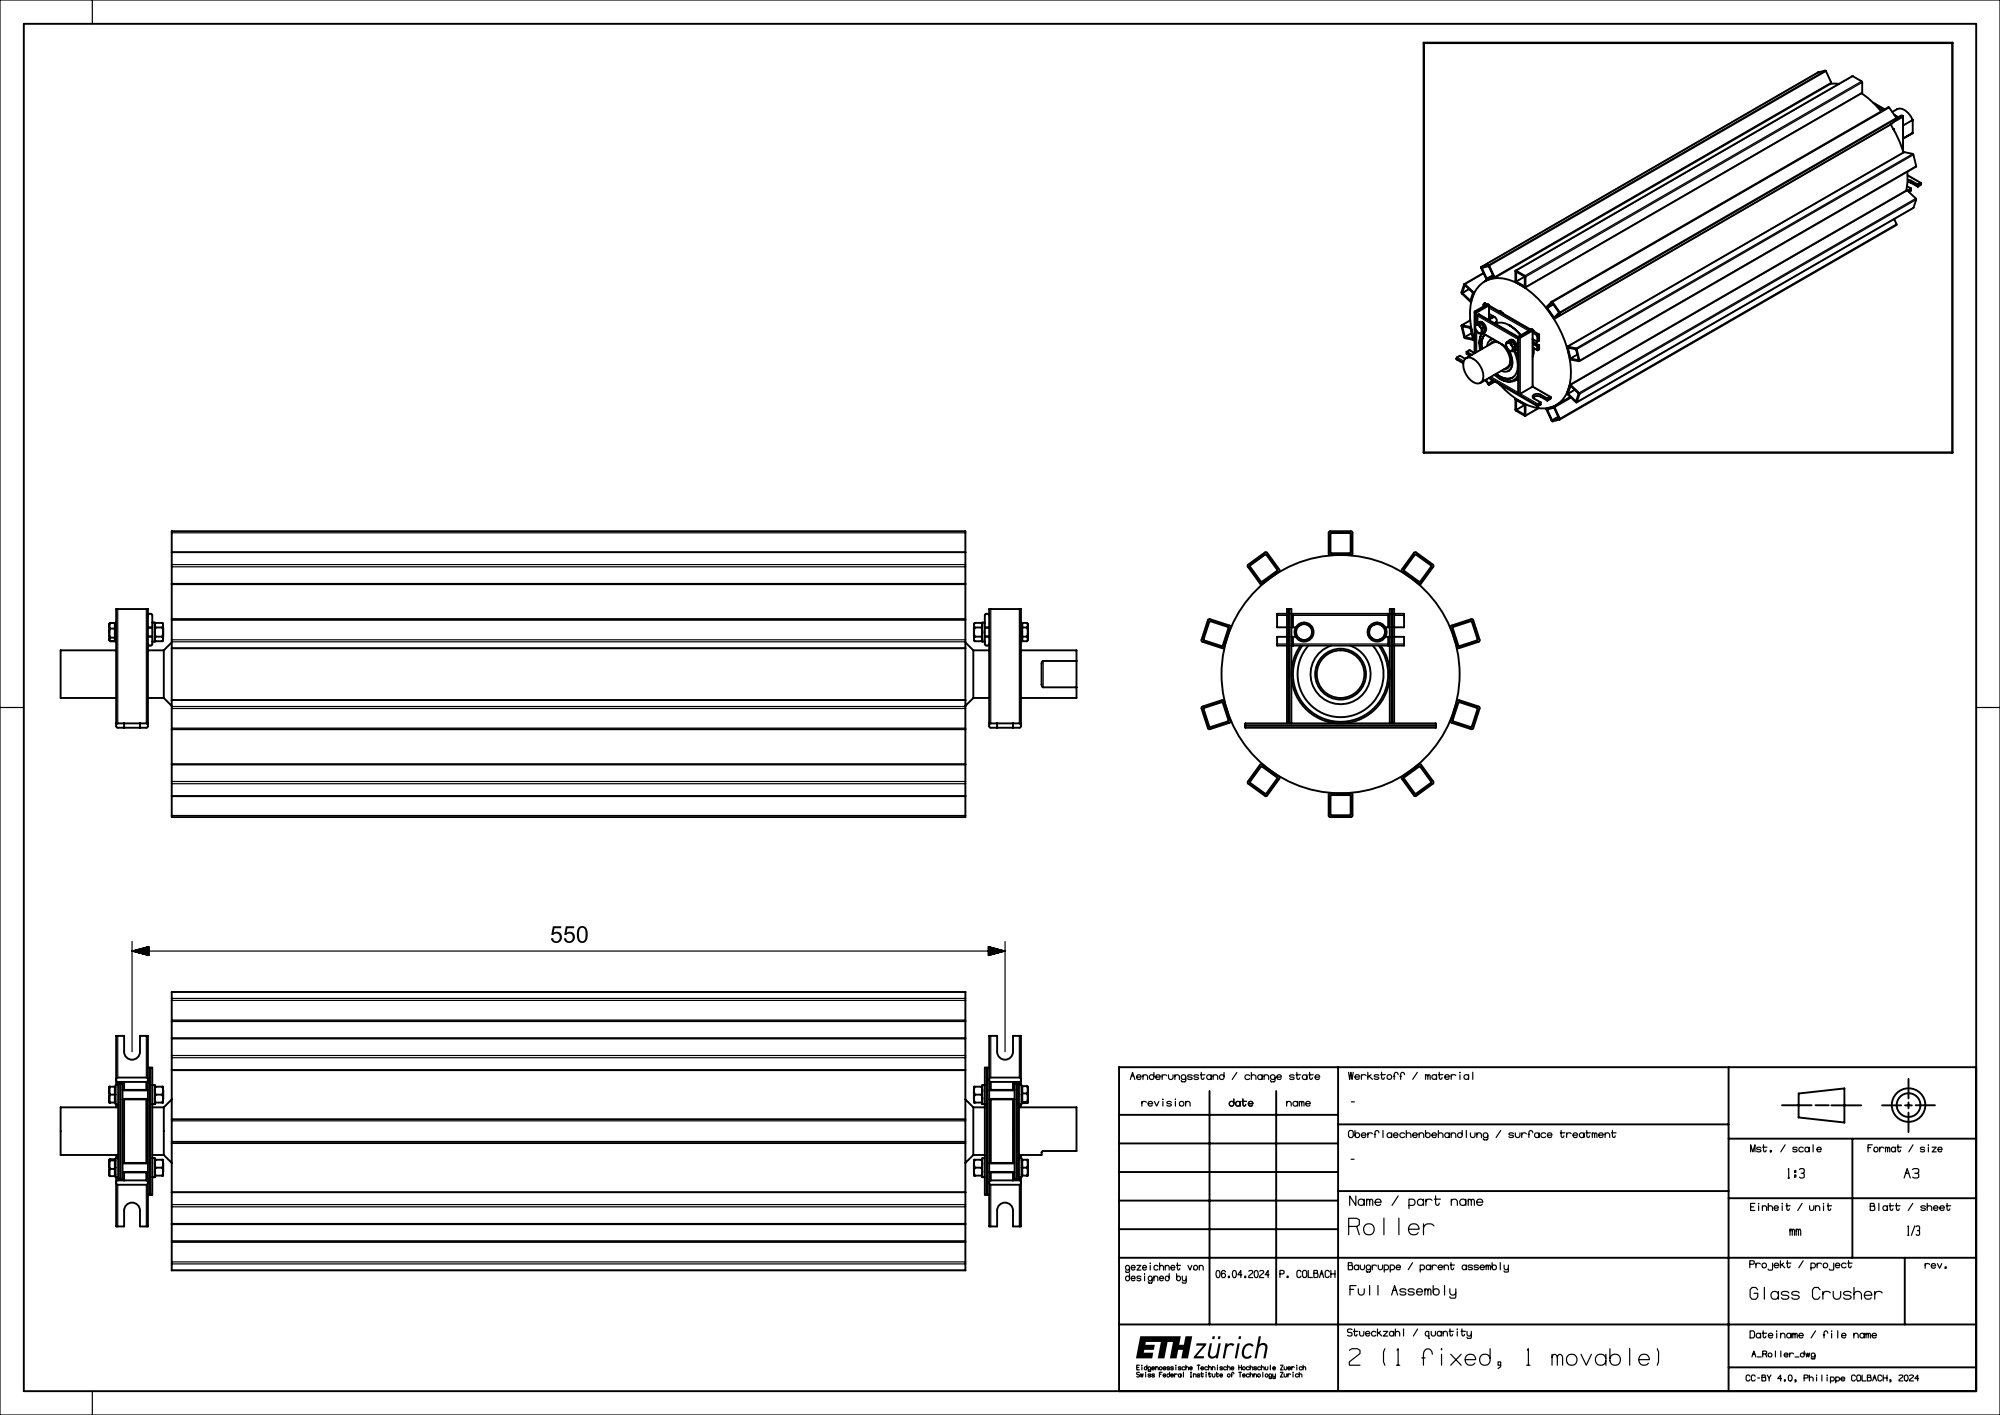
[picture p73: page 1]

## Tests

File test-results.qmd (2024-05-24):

---
title: "Results from Operation"
number-sections: true
format: html
---

# Overview

From the very beginning of the test stage, it became clear that the crusher was unable to break intact glass bottles. On the wide setting, which was specifically implemented for this purpose, the crusher did manage to pull in the bottles, but the exerted force was not high enough to crush them. The crank arm jammed up each time, and even though it felt physically possible to push it further, the drivetrain was suspected to get damaged before the bottle would. A sturdier drivetrain and an even larger gear ratio would certainly help mitigate the problem; however, there are limits to the availability of motorcycle sprocket sizes and to the clearance within the crusher’s drivetrain. Since a 2-layer compound gear train would be counterproductive for the sturdiness issues, a solution would likely require a fundamental redesign of the drivetrain. Therefore, the crusher was instead considered to be a fixed system, restricted to the narrowest setting only. This decision was facilitated by the fact that the process of adjusting the roller gap turned out rather cumbersome anyway.

# Glass crushing results

For testing the bottles were broken using a hammer before loading into the crusher. Figure 1 shows some examples for the state the glass was in before being inserted into the crusher. Figure 2 shows an example for the result after sorting; it more specifically depicts the shards produced form the batch in Figure 1 (c). The shards produced by the crusher were sorted into three categories: Small for shards smaller than 1 cm, medium for shards between 1 cm and 3 cm, and large for shards larger than 3 cm.

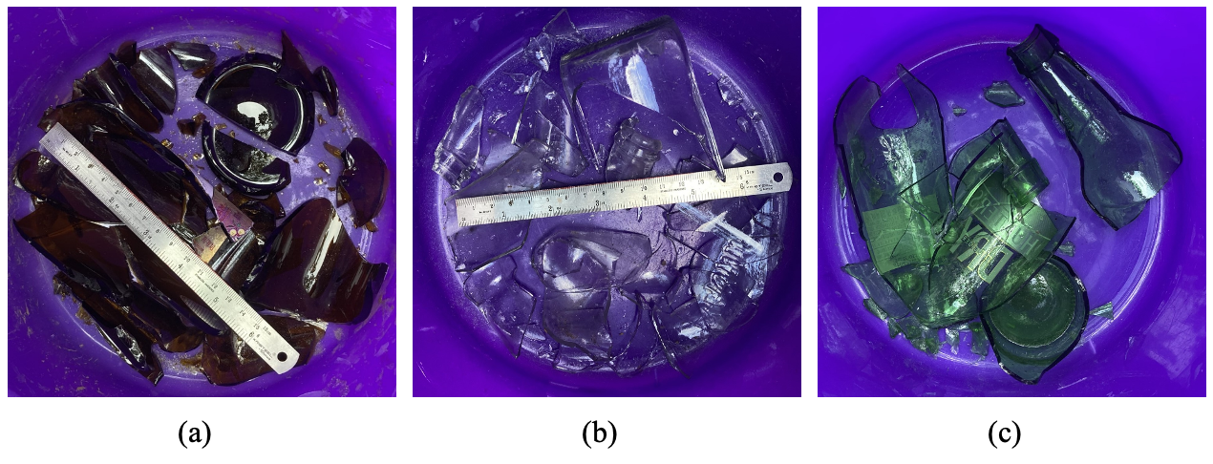
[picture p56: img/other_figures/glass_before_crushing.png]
Figure 1. Smashed glass bottles before passing through the crusher. Included in images (a) and (b) is a 15 cm ruler.


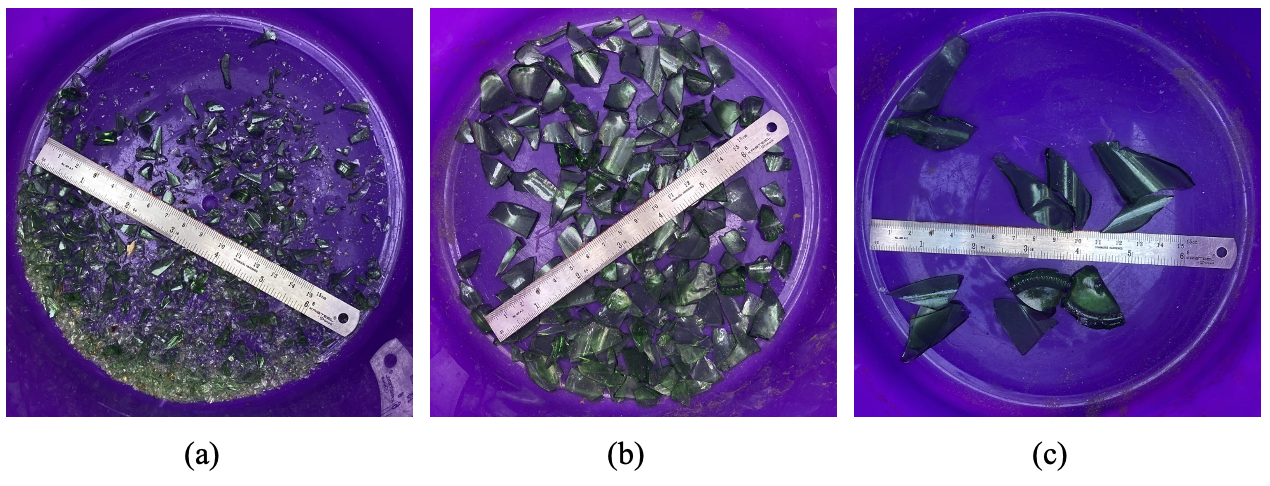
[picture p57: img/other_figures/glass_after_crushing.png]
Figure 2. Crushed glass sorted by size from small (a) to large (c) with a 15 cm ruler for scale.


As can be observed in Figure 3, there is some variation in the shard composition of the different batches, but overall, the medium category is always by far the predominant one, making up for 61 % to 77 % of the mass. There seems to be no clear trend regarding the percentages of small shards relative to the large ones, ranging from equal proportions to ratios slightly below 1:2 and vice versa. In short, with its single setting, the crusher is able to produce a variety of particle sizes ranging from powder to shards several centimeters long, but if one is only interested in a specific size, they have to be sieved first.

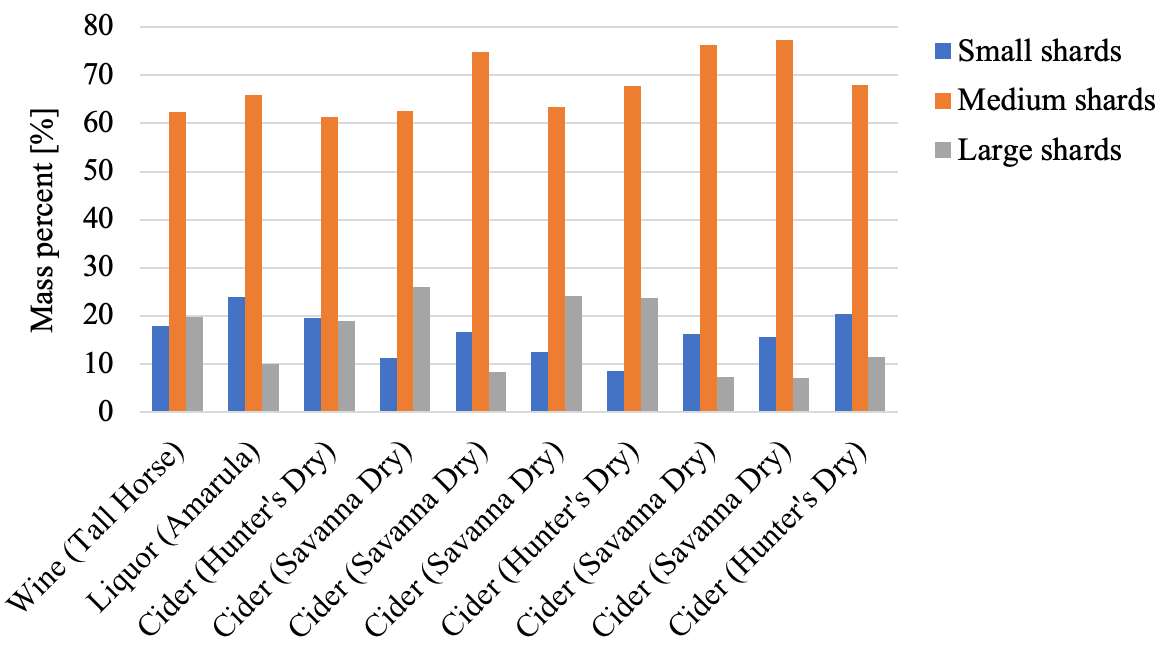
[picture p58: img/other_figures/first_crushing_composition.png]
Figure 3. Shard composition of the glass batches processed by the crusher.


To determine whether it makes sense to process the batches a second time to obtain a larger quantity of smaller shards, the large shards of the wine and liquor bottle were given a second pass through the crusher. Almost half of the wine bottle’s shards classified as small or medium afterwards, compared to only a quarter of the liquor bottle’s shards (Figure 4). Taking into account that the wine bottle’s shards were larger to begin with (Figure 5), thus decreasing their probability of getting through the crusher unscathed, this result is little surprising. In conclusion, repeated passes have diminishing benefits and are only worth the effort if the shards are still excessively large.

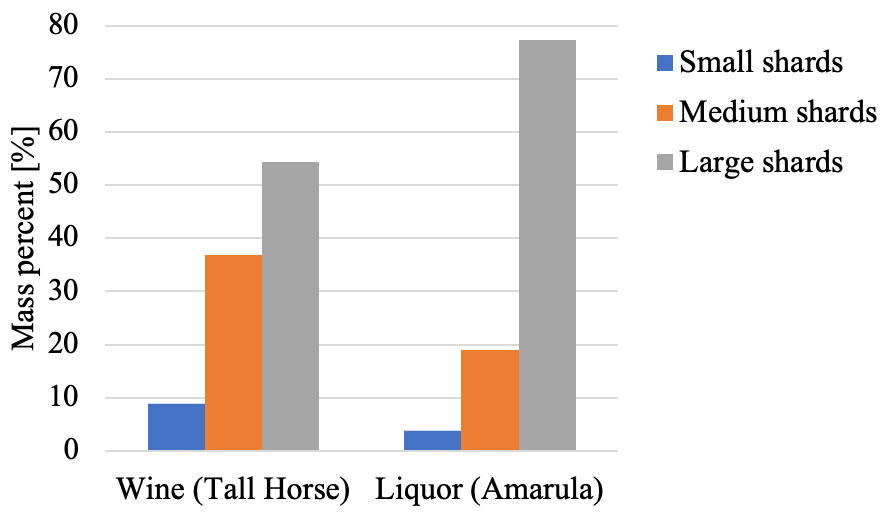
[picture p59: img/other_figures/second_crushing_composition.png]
Figure 4. Shard composition of the wine and liquor bottles’ large shards after giving them a second pass through the crusher.


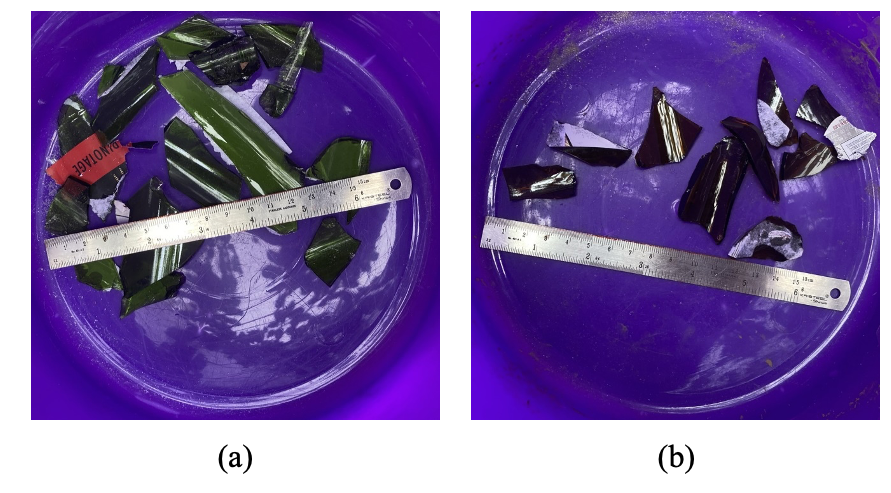
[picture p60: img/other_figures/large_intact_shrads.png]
Figure 5. The wine (a) and liquor (b) bottles' large shards after the first pass through the crusher.


On two occasions during testing, the crusher jammed when it encountered a particularly rigid piece of glass. The first time it was caused by the circa 9 mm thick base of a Jägermeister bottle during one of the crusher’s preliminary tests (Figure 6 (a)), the second time by the neck of a cider bottle (Figure 6 (b)). After removing them, the crushing process was resumed without issues.

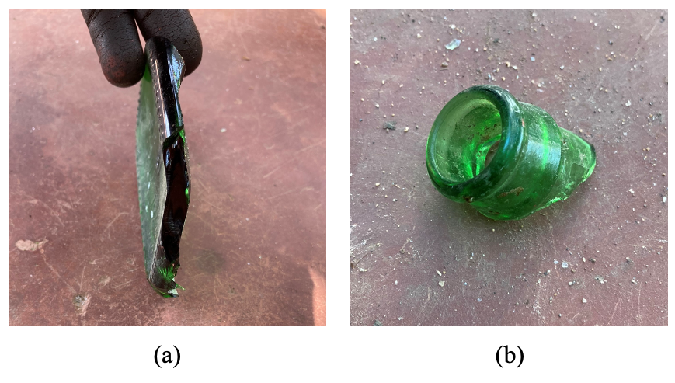
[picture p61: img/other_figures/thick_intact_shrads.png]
Figure 6. Base of the Jägermeister bottle (a) and neck of the cider bottle (b) that caused the crusher to jam.

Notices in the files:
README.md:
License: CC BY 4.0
